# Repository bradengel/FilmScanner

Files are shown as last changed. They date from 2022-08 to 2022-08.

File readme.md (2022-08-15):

# Film Scanner
This film scanner is based off of the very good work of Seckin Sinan Isik's LIDAR driven motorized film carrier here: https://www.duckafterduck.com/blog/how-to-make-a-lidar-driven-motorized-film-carrier

## Changes
- Moved CAD from FreeCAD to Fusion360
- Converted the main bodies (front and back) from surfaces to solid bodies (better for 3D printing)
- Removed the LIDAR mount (using modified software from https://github.com/bezineb5/RoboScan)
    - My fork here: https://github.com/bradengel/RoboScan?organization=bradengel&organization=bradengel
- Created 135 version
- Added Motor mount for 28BYJ-48 Stepper Motor
- Changed orientation to make extended film collectors the legs for horrizontal scanning
- Created a slot for plate glass to support film (WIP)
- Configured for bearings, rather than parts rubbing together

## Non-3D printed parts
- O-Rings
    - Nitrile Rubber O-Rings 16mm OD 11mm ID 2.5mm Width
    - https://www.amazon.com/dp/B07W61VVFV?psc=1&ref=ppx_yo2ov_dt_b_product_details
- Timing Belts
    - 110mm and 300mm GT2 6mm timing belt
    - https://www.amazon.com/dp/B07KK86NYX?psc=1&ref=ppx_yo2ov_dt_b_product_details
- Timing Belt Pulleys
    - 20 Tooth GT2x6mm 5mm bore
    - https://www.amazon.com/dp/B077GNZK3J?psc=1&ref=ppx_yo2ov_dt_b_product_details
- Stepper Motor and Driver
    - 28BYJ-48 Stepper Motor
    - ULN2003 Motor Driver
    - https://www.amazon.com/dp/B01CP18J4A?psc=1&ref=ppx_yo2ov_dt_b_product_details
- Ball Bearings
    - 625 Ball bearings 5mm x 16mm x 5mm
    - https://www.amazon.com/dp/B07TML6YP4?psc=1&ref=ppx_yo2ov_dt_b_product_details
- M4 bolts and nuts
    - 2x 10mm for stepper motor
    - 4x 15mm for spacers
- M4 Heat-set inserts
    - https://www.cnckitchen.com/shop#!/Gewindeeinsatz-threaded-insert-M4-Standard-50-Stk-pcs/p/431147582/category=0

## 3D Printed Parts
### Shared Components
- Drive Side Body (with stepper motor mount)
- Idle Side Body
- Film Collector (x2 for using as legs)

## non-shared components
- Drive and Idler axles
- Spacers

## A note about bearings, housings, shafts, and fits
Generally, you need to change the dimensions so that the fits on the bearings are what you want.  My dimensions may not work for you.  In a perfect world, I'd print the precision components on a resin printer (or even a metal 3d printer, then machine them to the proper tolerances), but I don't have one, nor do I want one.  So there.
### Bearing Housing Fit
My goals is to have the bearing housings (the holes that the bearings fit into on the drive and idle bodies) be interference fit (https://en.wikipedia.org/wiki/Interference_fit).  I've adjusted the dimensions so that _my_ 3D printer creates a housing that just barely fits the bearings.  I put the bearings in the freezer to shrink them, press them in their housing, and as they warm up, they expand into the housing.  This means that to remove the bearings, the body they are in will likely need to be destroyed, or you may try softening the plastic, but that could also melt the grease out of the bearings.
### Shaft Fit
Since the drive and idle bodies are shared, but the spacers and shafts are not, the bearing fit to the shafts should be a sliding clearance fit (https://en.wikipedia.org/wiki/Engineering_fit#Clearance_fits).  Again, I've adjusted the dimensions so that _my_ 3D outputs that result.

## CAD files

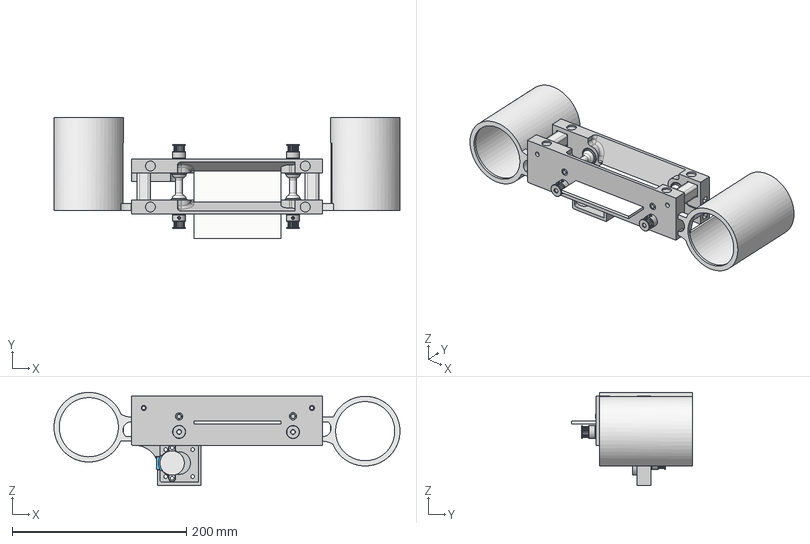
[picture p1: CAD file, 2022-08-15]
135 Scanner.step
397.5 x 139.0 x 107.1 mm
2GT-6 Belt Pulley 5mm x 5
Film Collector_2 x 2
135 Spacer x 2
O-Ring x 8
Drive Shaft x 2
Idler Shaft x 2
SKF_625_PART4 x 64
SKF_625_PART3 x 64
SKF_625_PART2 x 8
SKF_625_PART1 x 8
28BYJ_48_StepperBody
Plate Glass_1

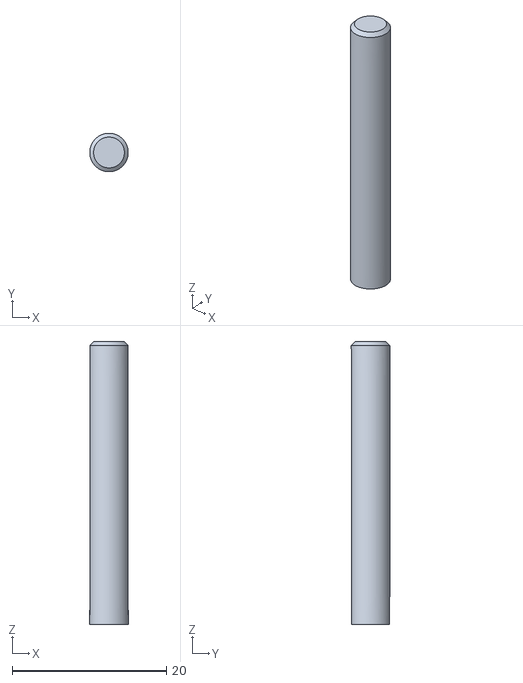
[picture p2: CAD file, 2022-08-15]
STL/120/120 Drive Shaft.stl
5.00 x 5.00 x 36.8

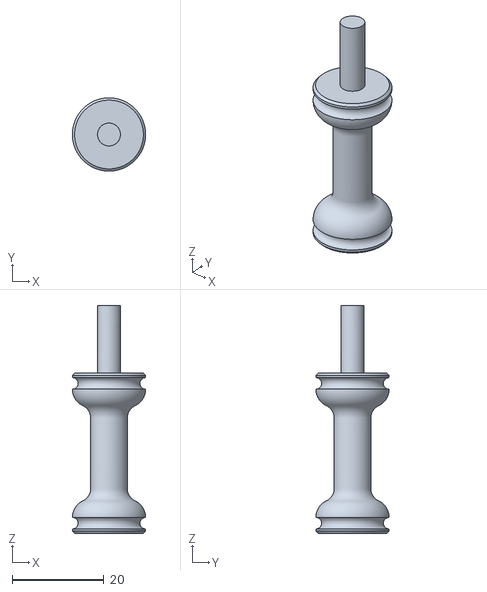
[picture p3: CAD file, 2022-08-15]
STL/135/135 Idler Axle.stl
16.0 x 16.0 x 49.7

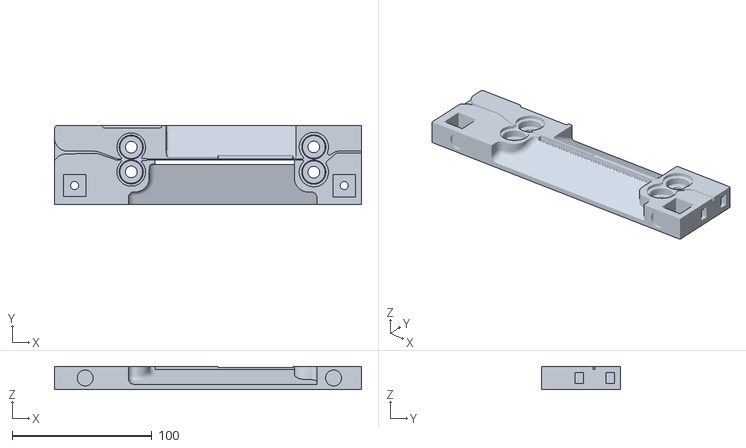
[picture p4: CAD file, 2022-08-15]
STL/Body Idle Side.stl
220.0 x 56.7 x 16.5

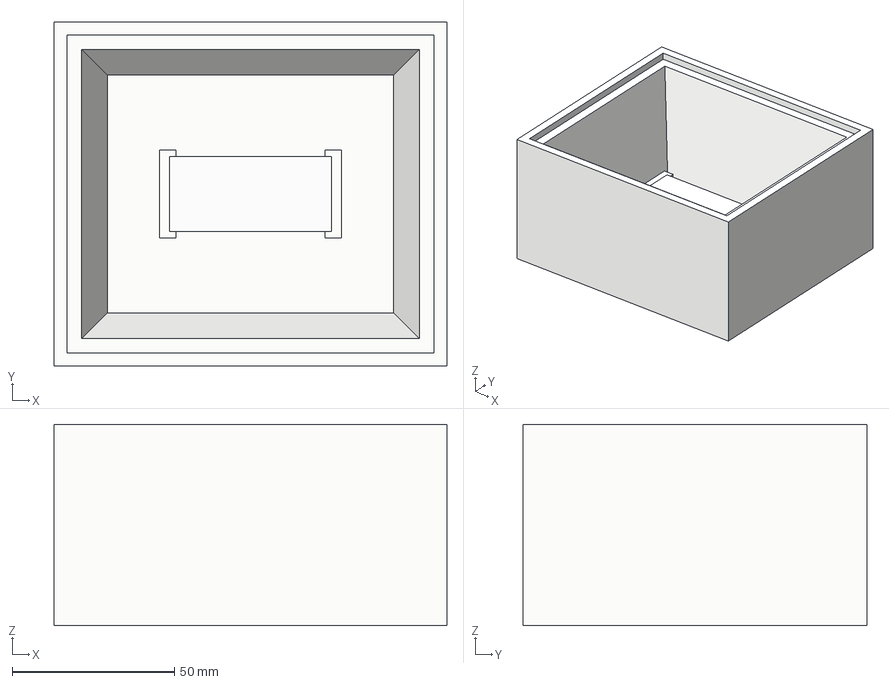
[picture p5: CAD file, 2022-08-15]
Light Box.step
121.0 x 106.0 x 62.0 mm
LED x 2
LED Sink

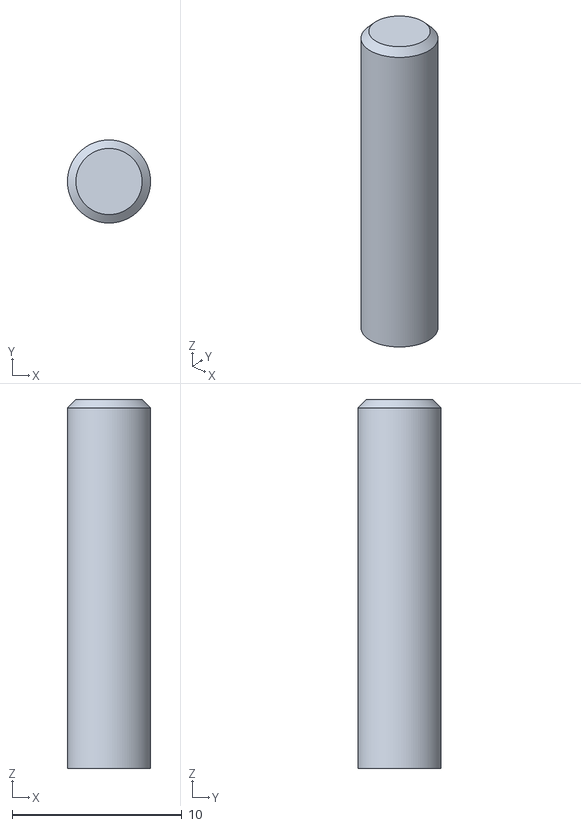
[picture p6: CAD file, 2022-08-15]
STL/120/120 Idler Shaft.stl
4.90 x 4.90 x 21.8

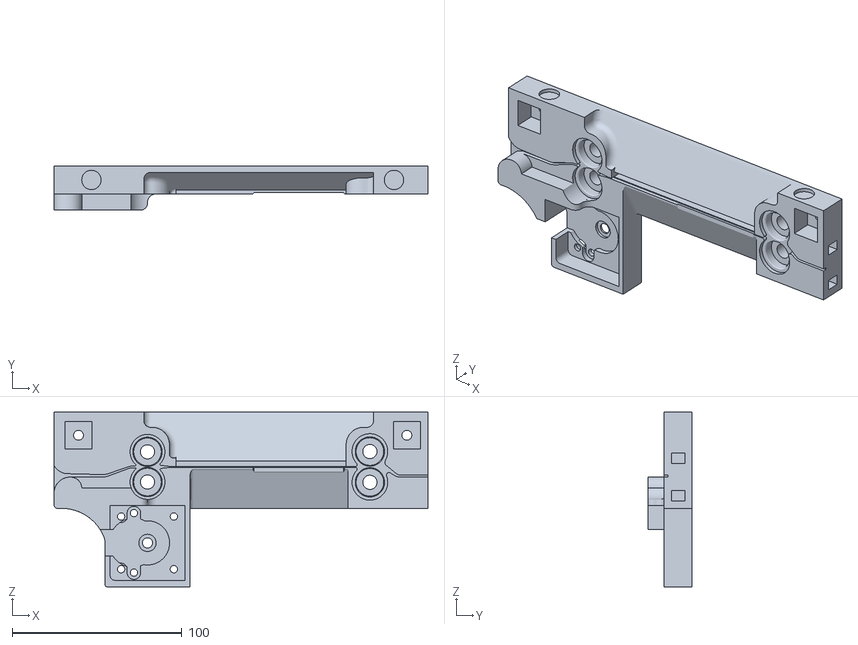
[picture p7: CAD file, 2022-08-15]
STL/Body Drive Side.stl
220.0 x 26.0 x 102.8

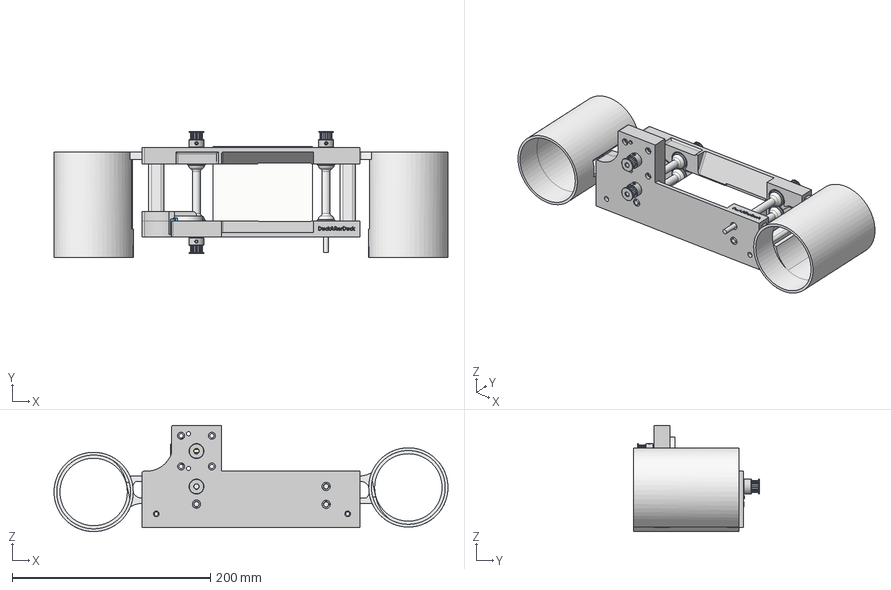
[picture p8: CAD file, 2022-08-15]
120 Scanner.step
397.5 x 127.4 x 107.1 mm
Film Collector_2 x 2
SKF_625_PART4 x 64
SKF_625_PART3 x 64
SKF_625_PART2 x 8
SKF_625_PART1 x 8
28BYJ_48_StepperBody
Spacer x 2
O-Ring x 8
Drive Shaft x 2
Idler Shaft x 2
2GT-6 Belt Pulley 5mm x 4
Plate Glass_1

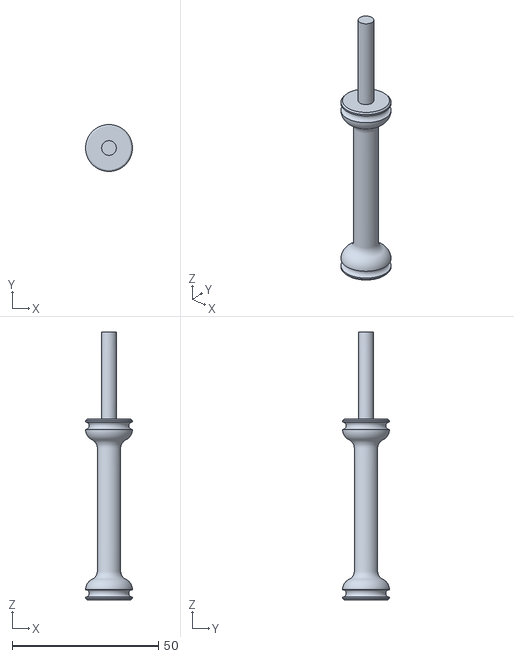
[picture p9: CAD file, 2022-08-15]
STL/120/120 Drive Axle.stl
16.0 x 16.0 x 91.5

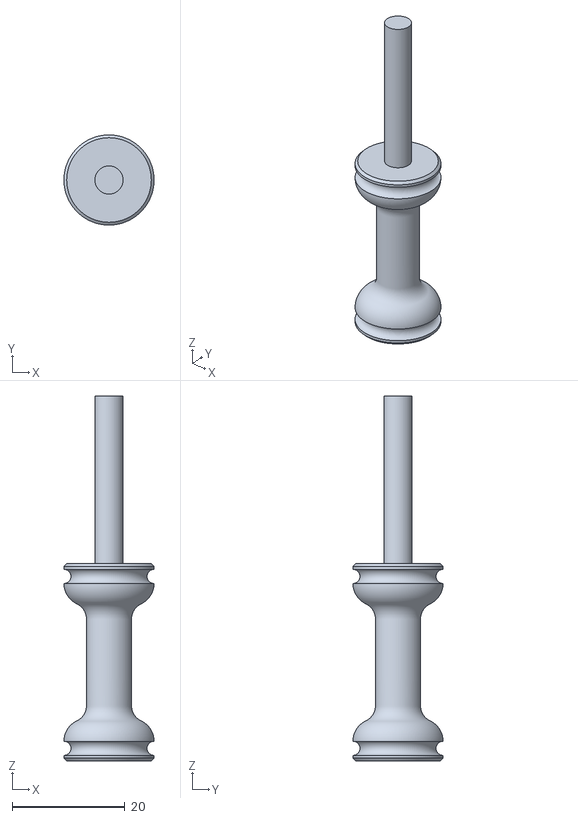
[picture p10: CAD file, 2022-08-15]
STL/135/135 Drive Axle.stl
16.0 x 16.0 x 64.7

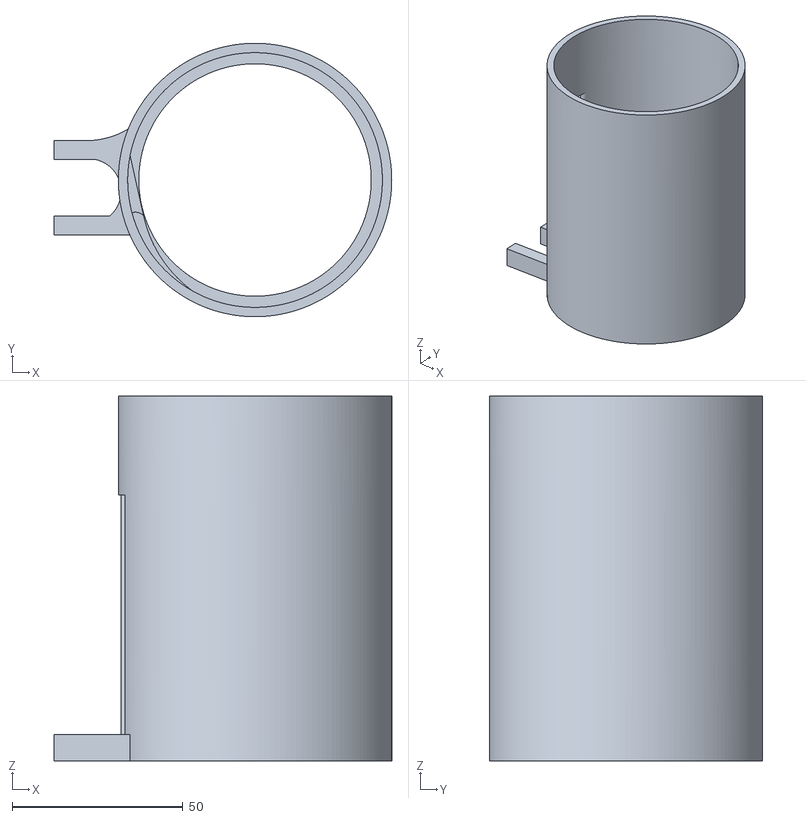
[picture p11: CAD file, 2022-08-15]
STL/Film Collector.stl
98.8 x 80.0 x 106.8

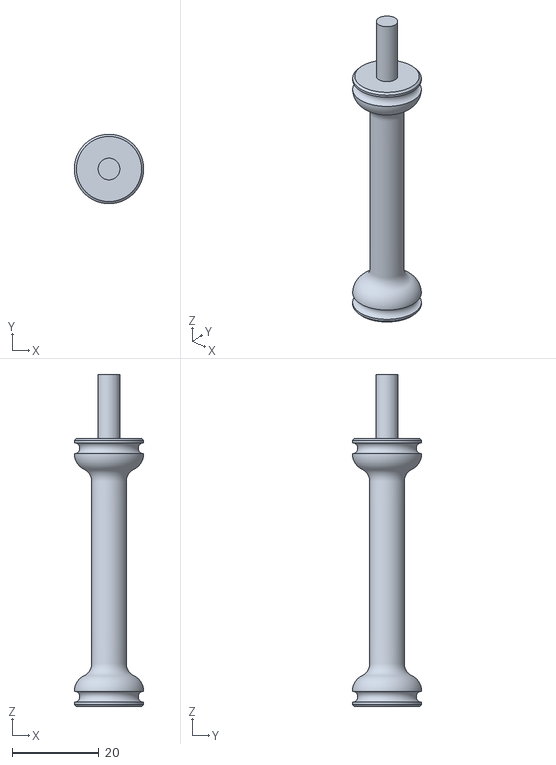
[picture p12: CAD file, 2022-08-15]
STL/120/120 Idler Axle.stl
16.0 x 16.0 x 76.5

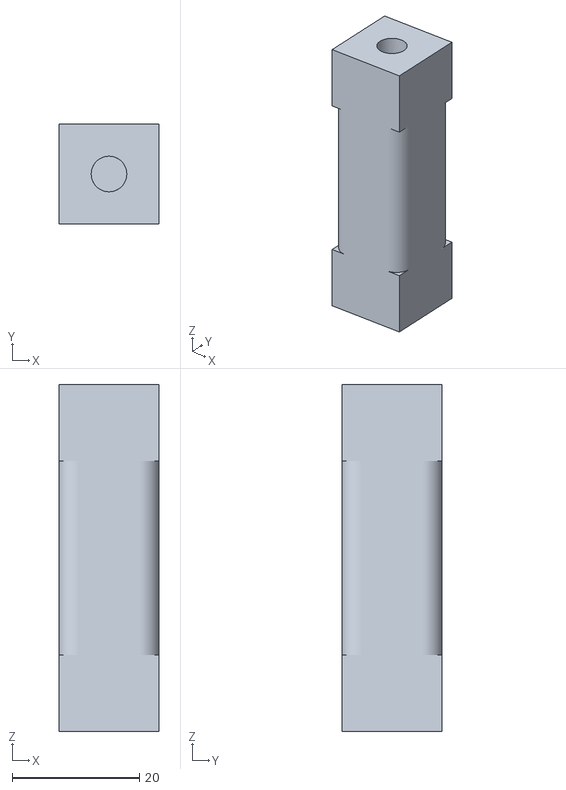
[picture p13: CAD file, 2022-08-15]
STL/135/135 Insert Spacer.stl
15.8 x 15.8 x 54.6

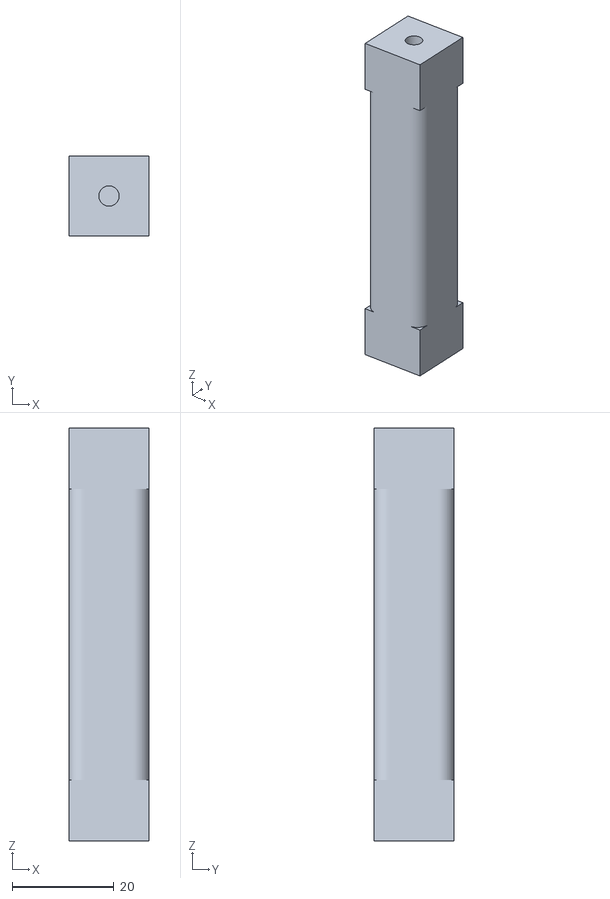
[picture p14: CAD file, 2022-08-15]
STL/120/120 Plastic Spacer.stl
15.8 x 15.8 x 81.3

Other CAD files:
STL/135/135 Drive Shaft.stl
STL/120/120 Threaded Insert Spacer.stl
STL/135/135 Plastic Spacer.stl
